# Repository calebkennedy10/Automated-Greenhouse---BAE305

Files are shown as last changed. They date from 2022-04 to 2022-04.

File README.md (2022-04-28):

# BAE305_Project_Greenhouse
## Summary
The purpose of this project is to utilize electronics and sensors to automate several greenhouse functions on a model scale as both a prototype for a full-size microcontroller-based automation system and as an educational model that can be used to demonstrate how an automated greenhouse works. Our team developed a sensor to detect light level and utilized an affordable off-the-shelf temperature and humidity sensor in order to direct automated heating, cooling, and lighting systems, as well as an automated irrigation system running on a timer. The main goals of the project were to create code that used sensor data to activate several of the systems both for demonstration purposes and actual utilizing of the greenhouse; to assemble a suitable greenhouse setup from a clear tub; and to organize the system in a way that would provide accurate data on greenhouse conditions. Each component was tested separately and as a whole, and the automated greenhouse was able to function as outlined in the project backlog.
## Design Description
### Supplies Needed
- SparkFun Electronics RedBoard DEV-13975
- Clear storage tub
- Adafruit 997 (Plastic Water Solenoid Valve - 12V -1/2" Nominal)
- ElectricSolenoidValves.com RSC-A2-12VDC (1/4" 12V DC Push Connect Plastic Solenoid Valve)
- MXC 1/4" Automatic Drip Mist Irrigation Kit (Model: GGOB)
- SparkFun Generic Servo Motors (ROB-09065)
- Bonsai wire
- Jumper wires (male-male and male-female)
- Electrical tape
- Plusivo Hook-up Wire Kit
- Photoresistor
- Ws2812 LED Matrix Panel
- DC 12V to 5V Converter
- 1/2" PVC pipe and various 1/2" fittings
- 10W 110V AC aquarium pump with 1/2" ID tubing output
- 1/2" ID tubing and barb fittings
- PVC cement and primer
- PLA filament
- 300W 12V power supply
- Solder
- Various crimp on electrical connectors (female disconnects, spade tongue, splices)
- 5 Gallon Bucket
- 2x Horizontal Float Switches
- 2x 12V PC fans
- Adafruit SHTC3 Temp and humidity sensor with wiring harness.
- 1/8W resistors (10K and 330)
- Fdit PTC Car Fan Air Heater for Small Room Space (12V 100W)
- TIP 31C Transistor 
- 12VDC, 30/40A Automotive Relay
- Bracket mount for relay
- Super glue

### 3D-Printed Components
All 3D printed componets are available via the "3D PRINTED PARTS" file in the repository.  They are available in their native SOLIDWORKS CAD formats.  Please refer to the assembly files in order to determine which parts are to be printed for each assembly and how the parts are assembled together.  3mm self tapping screws and 1/4"-20 bolts and nuts are the only pieces of hardware required to assemble each 3D printed assembly.  Parts can be printed out of several different materials and are designed to be printed on an FDM 3D printer.  Our team utilized Overture PLA Filament to print the parts; however, other common filaments types such as PETG, ABS, and ASA are acceptable if so desired.  All parts should be printed at a .2mm layer height with and infill density of 10%-15%.  It is advised to make spares of smaller parts such as the water emitters and servo attachments as these parts are easy to break during the assembly process.  Moving parts such as the vent flaps s will have to be sanded in order to allow for smooth rotation.  It is also recommended to drill out or sand holes where rotation will take place.  It is recommended to use a printer with a build plate area of at least 220mm x 220mm when printing large parts such as the vent flaps for the multivent.
### Circuit
While the circuit for this project is not overly complex, there is a lot of wiring involved.  Please refer to the schematic below when wiring up the system.  It is recommend that soldered connections with heat shrink coverings be utilized where possible in order to provide a water-tight seal around connections.  The power supply, voltage converter, microcontroller, breadboard, and relays should all be placed in a sealed container to protect them from the elements.  Our team utilized a 50W laser cutter to create a box to store all of these components.  If you have access to this type of tooling and wish to use our plans, the files for the box can be found in this repository.  Otherwise, any container or self-fabricated box will do as long as it provides adequate protection. 

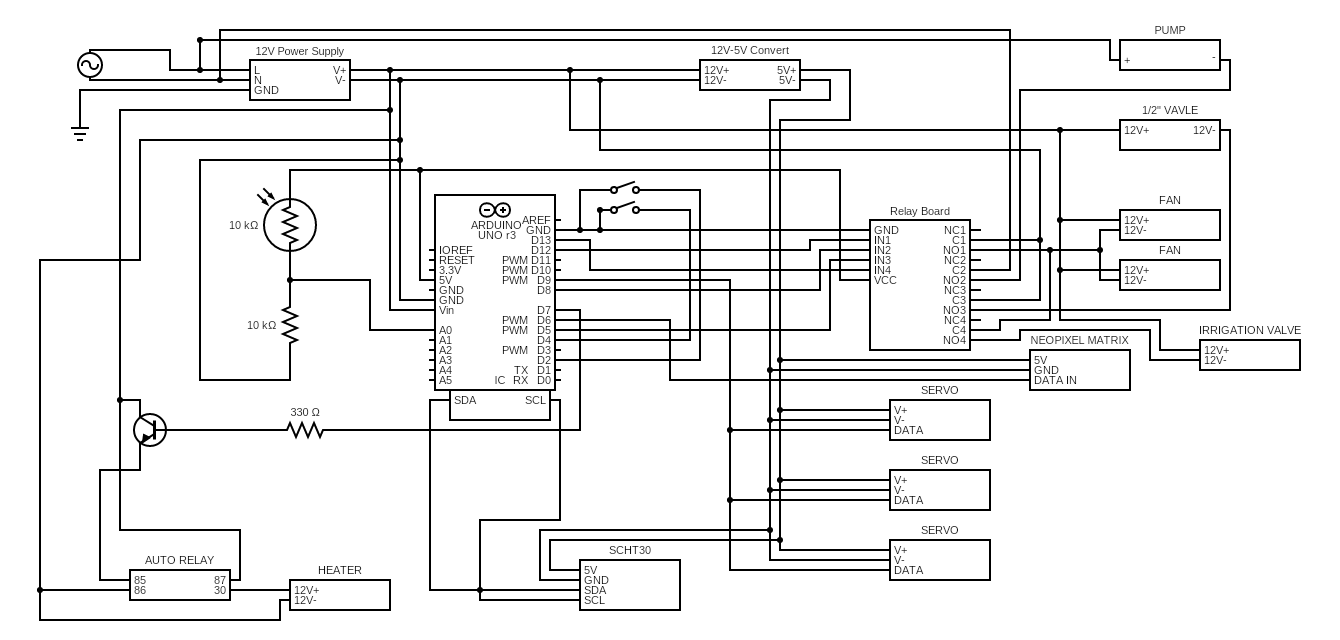
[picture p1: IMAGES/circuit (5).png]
Circuit Diagram


### Greenhouse Assembly
#### Cooling System
(The plumbing instructions for this section are intentionally a little vague.  There are multiple ways to plumb this system, and our team believes that it is best for plumbing system to be custom fabricated for each application of this design.)

Two vent fan assemblies and one evaporative cooling system assembly are required to complete the cooling system.  As mentioned previously, please refer to the SOLIDWORKS assembly files in order ot determine all 3D printed parts of the required to complete these assemblies.  The vent fan assemblies will be mounted on one end of the greenhouse while the evaporative cooling assembly will be mounted on the other side.  Assemble all sub assemblies prior to installation using 3mm screws.  Use the mounting adapters for the all of the assemblies to mark the holes that will need to be drilled in the house to mount the components.  All mounting holes will use 1/4"-20 hardware to hold components in place

Use the 5 gallon bucket to make a water sump for the evaporative cooling system.  Mount the pump at the bottom of the bucket.  Then mount a horizontal float switch 1 to 2 inches above the pump and mount another float switch approximately 6 inches below the top of the bucket.  Mount the 1/2" solenoid valve to the side of the bucket or in a pemanent location close by.  An input line that accepts a pressurized water source, such as a garden hose, will need to fabricated based on application needs.  An output line that runs from the valve to the inside of the sump will also need to be made.

For the vent fan assemblies, try to mount them as close to the center as possible to allow room for the servo mounts on the inside of the house.  One mounting adapter, the fan mount, fan, and fan retainer go on the exterior of the house while the other adapter, vent assembly, and servo mount go on the interior.  Once the proper orientation of the fan is decided on, drill a 5/16" hole in the fan mount to allow for the wires to pass through the wall of the mount.  This mounting procedure is to be utilized for both vent fan assemblies.

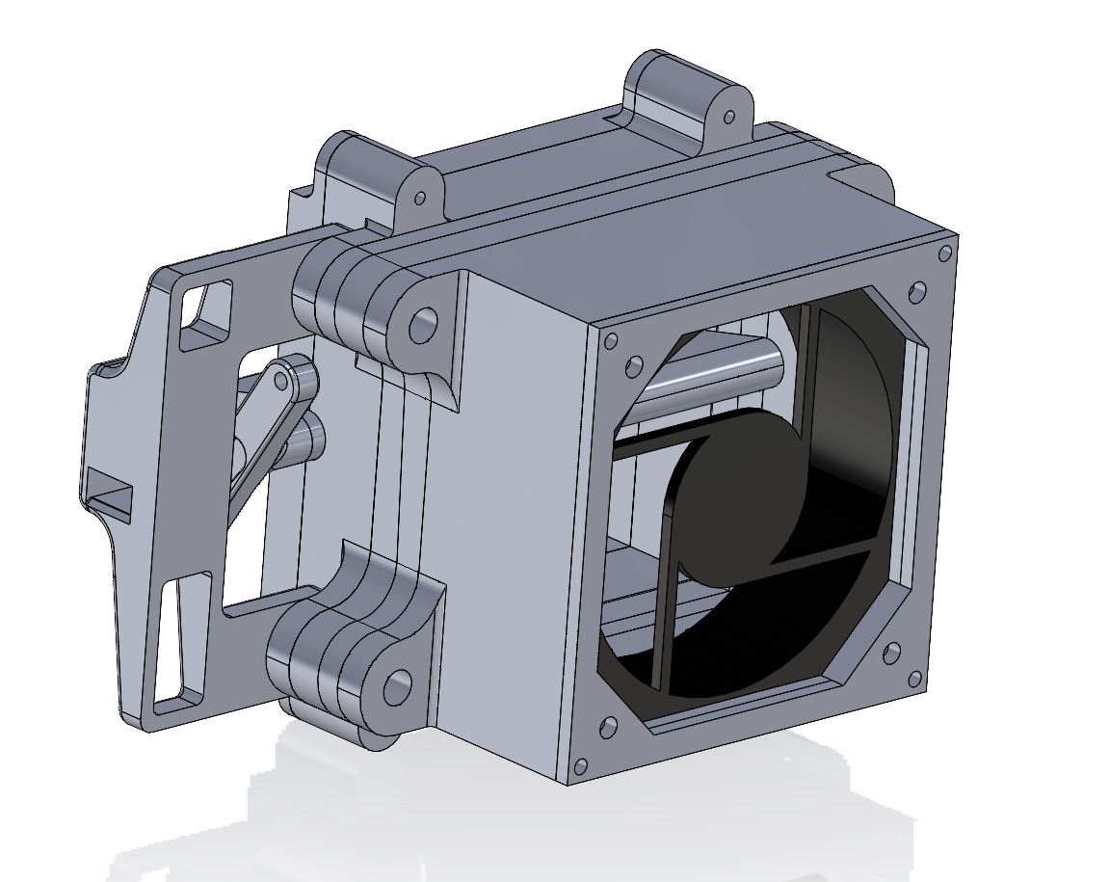
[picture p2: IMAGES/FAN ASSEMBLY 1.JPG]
Fan Assembly

(Fan Vent Assembly-Exterior View)
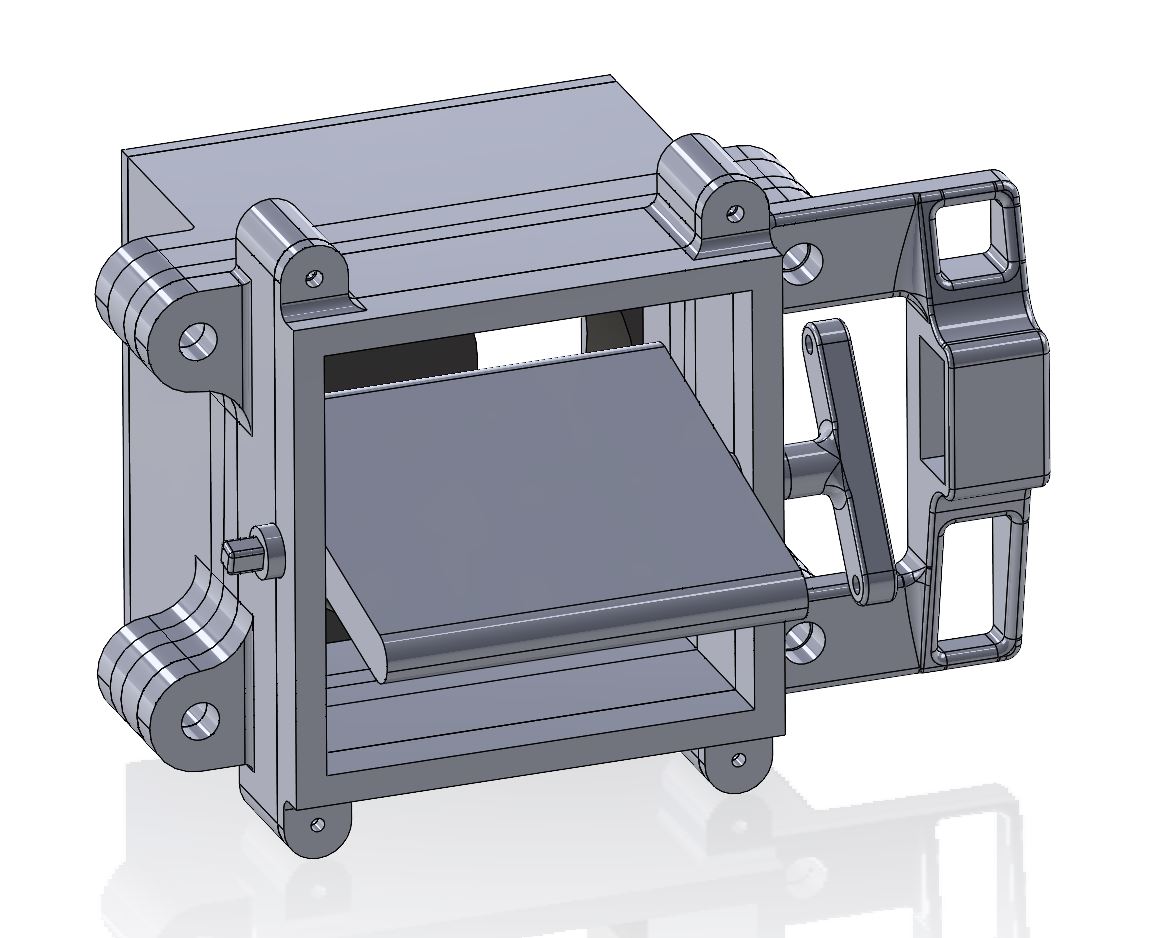
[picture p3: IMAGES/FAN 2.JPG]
Fan 2 Assembly

(Fan Vent Assembly-Interior View)

For the evaporative cooling system assembly, mount it as far to one side of the house as possible to allow for enough room for the servo mount on the inside.  The evaporative cooling wall assembly and one set of mounting adapters are mounted to the exterior of the greenhouse while the multi-vent assembly, servo mount, and last set of mounting adapters are mounted on the inside of the greenhouse.  The supply pipe for the evaporative cooling will need to fabricated using 1/2" PVC pipe, 15 Water Emitters, a PVC end cap, a slip joint-female thread pvc fitting, and male thread-1/2" barb fitting.  The 3/16 jig in the 3D printed parts folder can be used along with a cordless drill and 3/16" drill bit to drill the holes for the emitters.  The jig is used by inserting the peg into the first drilled hole and then drilling the next hole through the opening in the jig.  This process can be repeated for all 15 holes.  After drilling all of the holes, prep the pipe with primer, and insert the water emitters into the holes.  Use PVC cement on the emitter when placing them on the pipe to adhere them to the pipe and create a water tight seal.  Then slide the 3D printed pipe mounts onto both ends of the pipe.  Mount the pipe on the greenhouse and cut the ends to your desired length.  Then use the primer and cement to put on the rest of the fittings. 1/2" tubing will have to be ran from the pipe to the pump in the water sump; therefore, the last fitting on the pipe whould be a 1/2" barb fitting with a hose clamp
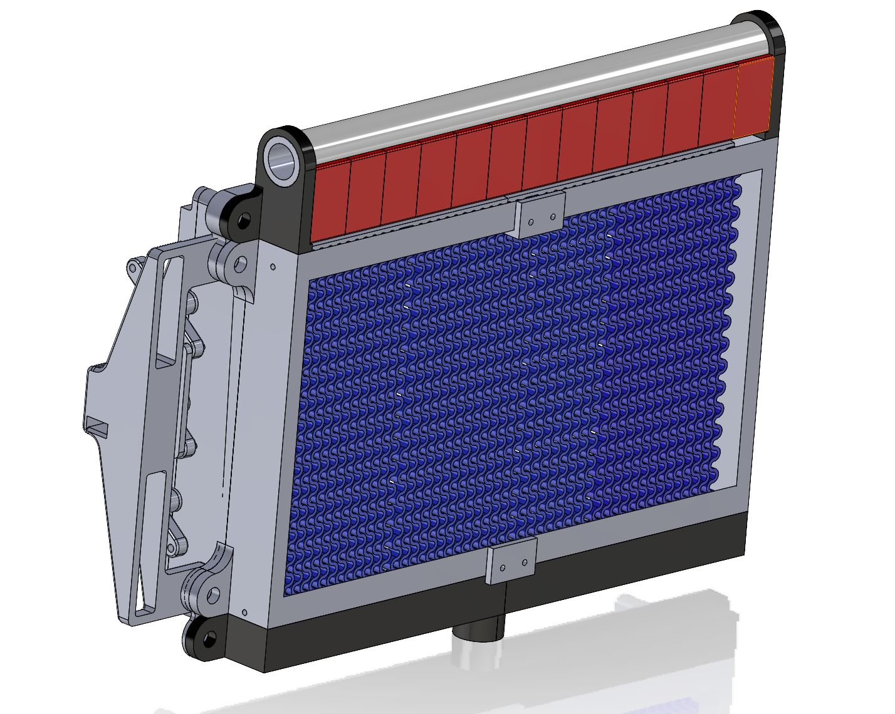
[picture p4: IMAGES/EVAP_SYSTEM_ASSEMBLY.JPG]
Evaporative Cooling Assembly

(Evaporative Cooling Assembly)

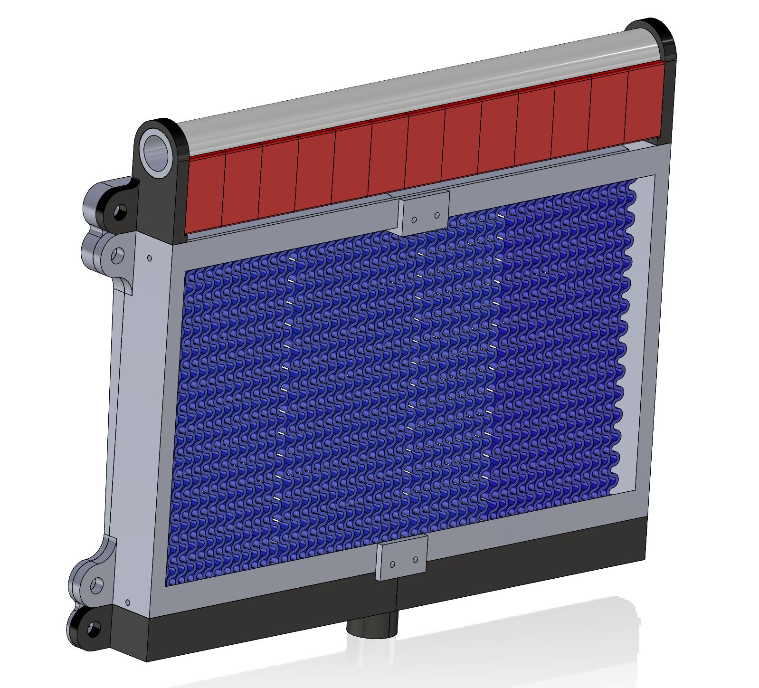
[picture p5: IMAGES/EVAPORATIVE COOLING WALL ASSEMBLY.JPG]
Evaporative Cooling Wall

(Evaporative Cooling Wall)

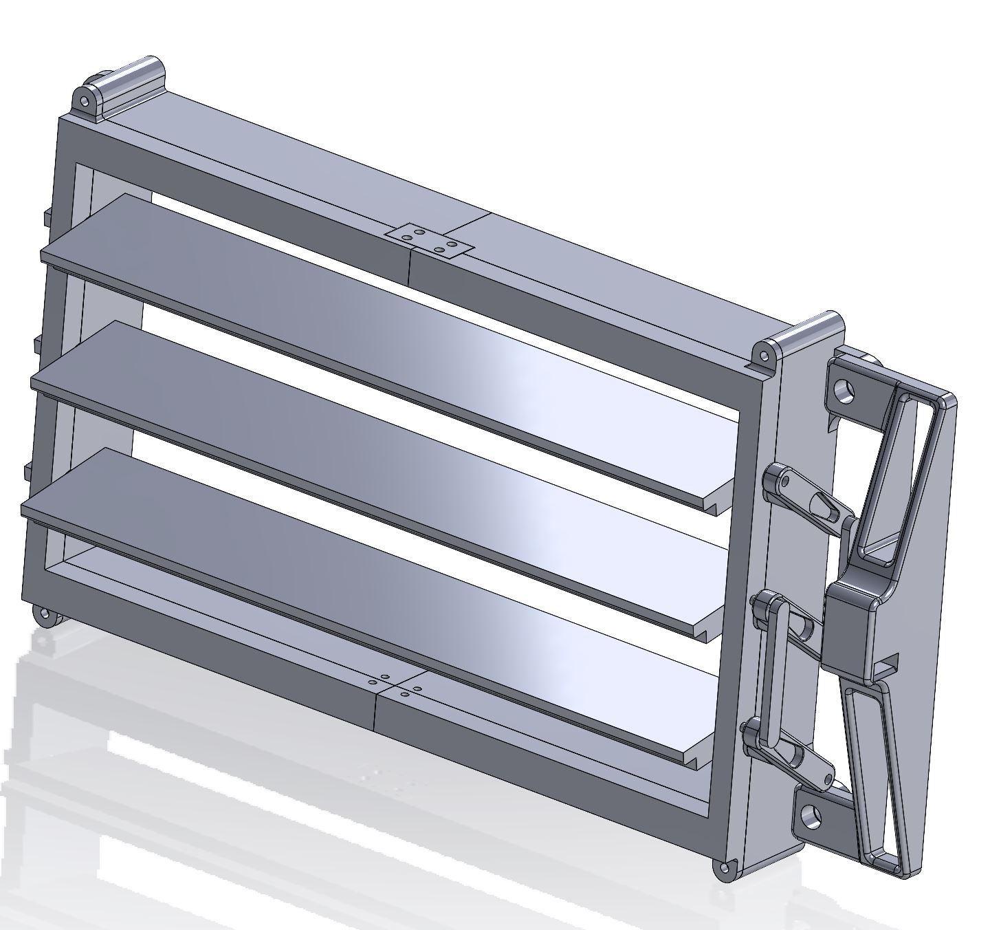
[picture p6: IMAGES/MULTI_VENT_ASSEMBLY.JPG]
Multi-Vent Assembly

(Multi-Vent Assembly)

Finally, use an Arduino to set three servo motors to 30 degrees.  Then press a servo arm into three 3D printed servo attachments.  Put the servo attachments on the ends of the vent flaps.  For the multi-vent assembly, a servo attachment will need to be added to both the lower and upper vent flap.  All three attachments will have to be connected using the vent links in the orientation shown by the picture above.  Once the links are in place, use a soldering iron to melt and expad the ends of the links to keep them from slipping out of the servo attachements.  Finally, mount all three servos using the servo mounts.
#### Heating System
The heater was purchased from amazon and consists of two parts: the electric heating element and fan. To simplify the wiring and to ensure that the fan and heating element would be on at the same time, the ground and power wires for each component were spliced together. The heater was mounted to the middle of the tub perpendicular to the cooling system using nuts and bolts, which allows for the cooling system to have ample space. Other components associated with system was a TIP 31C transistor, 1kΩ resistor, and an automotive relay (12 VDC, 40A) and are housed in the electronics housing. The automotive relay’s 85 output pin is wired to the transistor's middle pin on the breadboard and then the transistor's base pin is wired to the Arduino so that the heating system can be controlled. The system required various crimp on electrical connectors such as female disconnects, splices, and spade tongues to wire these components together. This system is wired according to the provided schematic above.
#### Lights
The parts needed for the lighting system are the Ws2812 LED matrix panel, DC 12V to 5V converter, photoresistor, wires, a resistor, 12V power supply, and Arduino. The voltage converter and Arduino are placed in the electronics housing. The LED matrix is or glued in place on the top exterior of the greenhouse. Two 1/16-inch holes are drilled into the top of the of the electronics housing. The two photoresistor wire ends are put through these two holes with the light sensing part of the photoresistor on the exterior. The other resistor is placed on the Arduino breadboard. All the components are wired according to the schematic.
#### Sensors
The sensor systems for this project is rather simple.  The first system is a voltage divider that uses a photoresistor to act as a light detection system.  The voltage divider is supplied with 5V that passes through the photoresistor then a 10k ohm resistor which is connected to ground.  A jumper wire is connected at the node between the two resistors and is connected to the A2 pin on the microcontroller.  The controller collects the data from this sensor using the analogRead command and stores it in a variable that can be compared to a constant in order to determine if the lighting system should be on or off.  The photoresistor itself should be placed in a fully exposed area in order to properly monitor the sunlight level.  For our application, we placed it on the top of our electronics box.

The second sensor is the Adafruit SHTC3.  This sensor is a compact temperature humidity sensor that utilizes a simple JST wiring harness and I2C communication protocol.  Adafruit has a library developed specifically for this sensor that allows for quick and easy data collection via the I2C ports on the SparkFun Redboard.  The data collected from the sensor is converted to an integer type variable that can be used in logic statements to determine which controlled environment systems should be turn on or off in order to maintain the optimum in door conditions for plant growth.  The sensor was mounted to the inside of the greenhouse using the 3D printed temp sensor mount, 3mm self-tapping screws, and super glue.  The sensor was screwed on to the mount.  Then the back of the mount was glued to the inside wall of the greenhouse close to the exhaust fans.

#### Irrigation
The irrigation system consists of a 1/4" 12V DC plastic solenoid valve, as well 15 feet of 1/4" diameter tubing, 18 adjustable mister nozzles, 20 flat tee fittings, and a 3/4"-1/4" faucet adapter from the MXC Automatic Drip Mist Irrigation Kit. It is split into three lines across the length of the ceiling of the greenhouse, which are attached via twelve loops of bonsai wire strung through pairs of holes drilled into the ceiling. Each line contains 6 mister nozzles, which are attached to flat tees with 1/2" lengths of tubing; tubing is also used to string the flat tees together in order to create an irrigation line. 2 other flat tees are used to connect the lines to each other and to the tubing that goes to the solenoid valve. All connection of tubing to tees should be done using a butane torch to soften the tubing for easier insertion. The solenoid valve can also be connected to the faucet adapter via a portion of tubing, and then wired to the power supply and relay using male-to-female jumper wires. The wires should be soldered to the tabs on the valve: the left wire to power and the right to the relay. The faucet adapter should be used to connect the irrigation to an outside water supply, such as a faucet or hose.

### Code

#### Demo Code

This code was designed to test and demonstrate the functioning of the different subsystems. This was done so there was not a need for a change in the environment for the sensors to pick up on to turn on the different subsystems. To do this, a serial monitor was set up. It asked for the desired temperature and humidity, and status of lights and irrigation. Based on these inputs, logic if-else statements turned on or off the different subsystems. This allowed for easy turning on or off of the different subsystems to see or show if they worked individually and all together. 

`#include <Servo.h>`

`String temperature;`

`String RH;`

`String light;`

`String irrigation;`

`int temperatureInput;`

`int RHInput;`

`int lightInput;`

`int irrigationInput;`

`int lowWaterPin = 2;`

`int highWaterPin = 4;`

`int refillValve = 5;`

`int heaterPin = 7;`

`int pumpPin = 8;`

`int fanPin = 12;`

`int irrigationPin = 13;`

`int ventOne = 9;`

`Servo servoOne;`

`#include <Adafruit_NeoPixel.h>`

`#ifdef __AVR__`

`  #include <avr/power.h>`

`#endif`

`#define LED_PIN 3`

`#define NUMPIXELS 64`

`Adafruit_NeoPixel pixels(NUMPIXELS, LED_PIN, NEO_GRB + NEO_KHZ800);`

`#define DELAYVAL 500`

`void setup() {`

`  // put your setup code here, to run once:`

`  #if defined(__AVR_ATtiny85__) && (F_CPU == 16000000)`

`  clock_prescale_set(clock_div_1);`

`  #endif`

`  pixels.begin();`

`  pinMode(lowWaterPin, INPUT_PULLUP);`

`  pinMode(highWaterPin, INPUT_PULLUP);`

`  pinMode(refillValve, OUTPUT);`

`  // pinMode(LEDPin, OUTPUT);`

`  pinMode(heaterPin, OUTPUT);`

`  pinMode(pumpPin, OUTPUT);`

`  pinMode(fanPin, OUTPUT);`

`  pinMode(irrigationPin, OUTPUT);`

`  digitalWrite(refillValve, HIGH);`

`  digitalWrite(heaterPin, LOW);`

`  digitalWrite(pumpPin, HIGH);`

`  digitalWrite(fanPin, HIGH);`

`  digitalWrite(irrigationPin, HIGH);`

`  servoOne.attach(ventOne);`

` // servoTwo.attach(ventTwo);`

` // servoThree.attach(ventThree);`

`  servoOne.write(120);`

 `// servoTwo.write(0);`

 `// servoThree.write(0);`

 ` Serial.begin(9600);`

 ` Serial.println("Enter demo parameters.");`

 ` Serial.println("Seperate parameter values with commmas. Only input integers");`

 ` Serial.println("Input order: Temperature, Relative Humidity, Light Status, Irrigation Status");`

 ` Serial.println("Appropriate input values:");`

 ` Serial.println("  Temperature: Anything in Degrees Fahrenheit");`

 ` Serial.println("  Relative Humidity: 0-100");`

 ` Serial.println("  Light Status: 1 = Turn on, 0 = Turn off");`

 ` Serial.println("  Irrigation Status: 1 = Turn on, 0 = Turn off");`

 ` Serial.println("Example Input: 80,60,1,1");`

`}`

`void loop() {`

`  // put your main code here, to run repeatedly`

`  if (Serial.available()>0) {`

`    temperature = Serial.readStringUntil(',');`

`    RH = Serial.readStringUntil(',');`

`    light = Serial.readStringUntil(',');`

`    irrigation = Serial.readStringUntil(',');`

`    temperatureInput = temperature.toInt();`

`    RHInput = RH.toInt();`

`    lightInput = light.toInt();`

`    irrigationInput = irrigation.toInt();`

`      if (lightInput == 1) {`

`        pixels.fill(pixels.Color(255, 0, 255), 0, 64);`

`        pixels.show();    `

`      }`

`      else {`

`        pixels.fill(pixels.Color(0, 0, 0), 0, 64);`

`        pixels.show();`

`      }`

`      if (irrigationInput == 1) {`

`        digitalWrite(irrigationPin, LOW);`

`      }`

`      else {`

`        digitalWrite(irrigationPin, HIGH);`

`      }`

`      if (lowWaterPin == HIGH) {`

`        digitalWrite(refillValve, LOW);`

`          while (highWaterPin==HIGH) {`

`            delay(1000);`

`          }`

`        digitalWrite(refillValve, HIGH);  `

`      }`

`      if (temperatureInput > 85) {`

`        servoOne.write(30);`

`        delay(2500);`

`        digitalWrite(fanPin, LOW);`

`        digitalWrite(pumpPin, LOW);`

`        digitalWrite(heaterPin, LOW);`

`      }`

`      else if (temperatureInput > 75 & RHInput< 50){`

`        servoOne.write(30);`

`        delay(2500);`

`        digitalWrite(fanPin, LOW);`

`        digitalWrite(pumpPin, LOW);`

`        digitalWrite(heaterPin, LOW);`

`      }`

`      else if (temperatureInput > 75) {`

`        servoOne.write(30);`

`        delay(2500);`

`        digitalWrite(fanPin, LOW);`

`        digitalWrite(heaterPin, LOW);`

`        digitalWrite(pumpPin, HIGH);`

`      }`

`      else if (temperatureInput < 55) {`

`        servoOne.write(120);`

`        delay(2500);`

`        digitalWrite(heaterPin, HIGH);`

`        digitalWrite(fanPin, HIGH);`

`        digitalWrite(pumpPin, HIGH);`

`      }`

`      else{`

`        servoOne.write(120);`

`        delay(2500);`

`        digitalWrite(fanPin, HIGH);`

`        digitalWrite(heaterPin, LOW);`

`        digitalWrite(pumpPin, HIGH);`

`      }`

`}`

`}`

#### Automation Code

This is the true automation code for the greenhouse.  This code builds off of the demo code’s logic to create an automated system by utilizing sensor readings to control subsystems rather than utilizing a manual input from the operator.  Once again, the sensors that are utilized are the Adafruit SHTC3 temperature and humidity sensor, which operates using the I2C communication protocol, and a voltage divider circuit that utilizes a photoresistor to vary the analog input read by the Arduino according to the exterior lighting conditions.  The data collected from these sensors are stored in integer variables that are applied to logic base if, else if, and else statements to determine whether the cooling, heating, and lighting systems come on.  The irrigation system was automated through the use of a simple algorithm that use the milllis() Arduino function to turn on the irrigation system for one minute every six hours.  These intervals can easily be changed by modifying a couple of variables at the start of the code.  All variables that are utilized within in this code use a naming scheme that allows the operator to easily determine the data that is stored in the variable in order to allow for quick modifications to be made to the code in order to meet the operator’s needs.

`// variable setup`

`#include <Servo.h>`

`#include "Adafruit_SHTC3.h"`

`Adafruit_SHTC3 shtc3 = Adafruit_SHTC3();`

`#include <Adafruit_NeoPixel.h>`

`#ifdef __AVR__`

  `#include <avr/power.h>`
  
`#endif`

`#define LED_PIN 3`

`#define NUMPIXELS 64`

`Adafruit_NeoPixel pixels(NUMPIXELS, LED_PIN, NEO_GRB + NEO_KHZ800);`

`#define DELAYVAL 500`

`int tempSensPin = A0;
`
`int RHSensPin = A1;`

`int lightSensPin = A2;`

`int irrigationTime = 1;`

`int irrigationInterval = 360;`

`int irrigationStatus = 0;`

`int hours = 0;`

`int minutes1 = 0;`

`int minutes2 = 0;`

`int timePast = 0;`

`int lightThreshold = 550;`

`int temperature = 70;
`
`int humidity1 = 60;`

`int lowWaterPin = 2;`

`int highWaterPin = 4;`

`int refillValve = 5;`

`int heaterPin = 7;`

`int pumpPin = 8;`

`int fanPin = 12;`

`int irrigationPin = 13;`

`int ventOne = 9;`

`Servo servoOne;`

`void setup() {`

  `// put your setup code here, to run once:`
  
  `#if defined(__AVR_ATtiny85__) && (F_CPU == 16000000)`
  
  `clock_prescale_set(clock_div_1);`
  
  `#endif`
  
  `pixels.begin();`
  
  `pinMode(lowWaterPin, INPUT_PULLUP);`
  
  `pinMode(highWaterPin, INPUT_PULLUP);`
  
  `pinMode(refillValve, OUTPUT);`
  
  `pinMode(heaterPin, OUTPUT);`
  
  `pinMode(pumpPin, OUTPUT);`
  
  `pinMode(fanPin, OUTPUT);`
  
  `pinMode(irrigationPin, OUTPUT);`

  `digitalWrite(refillValve, HIGH);
  `
  `digitalWrite(heaterPin, LOW);`
  
  `digitalWrite(pumpPin, HIGH);
  `
  `digitalWrite(fanPin, HIGH);`
  
  `digitalWrite(irrigationPin, HIGH);`
  
  `servoOne.attach(ventOne);`

  `servoOne.write(120);`

  `Serial.begin(9600);`

  `while (!Serial)`
  
  `delay(10);     // will pause Zero, Leonardo, etc until serial console opens`

  `Serial.println("SHTC3 test");`
  
  `if (! shtc3.begin()) {`
  
  `Serial.println("Couldn't find SHTC3");`
  
  `while (1) delay(1);`
  
  `}`
  
  `Serial.println("Found SHTC3 sensor");`
  
  `Serial.println(irrigationInterval);`
`
}`

`void loop() {`

`// put your main code here, to run repeatedly:`

  `sensors_event_t humidity, temp;`

`shtc3.getEvent(&humidity, &temp);// populate temp and humidity objects with fresh data`

`lightSensPin = analogRead(A2); `

`Serial.println(lightSensPin);`

  `if (lightSensPin < lightThreshold){`

`pixels.fill(pixels.Color(255, 0, 255), 0, 64);`

`pixels.show(); `

`}`

`else {`

`pixels.fill(pixels.Color(0, 0, 0), 0, 64);`

`pixels.show();`

`}`

`if (lowWaterPin == HIGH) {`

`digitalWrite(refillValve, LOW);`

`while (highWaterPin== HIGH) {`

`delay(1000);`

`}`

`digitalWrite(refillValve, HIGH);  `

`}`

`temperature = temp.temperature;`

`humidity1 = humidity.relative_humidity;`

`Serial.println(temperature);`

`Serial.println(humidity1);`
   
`if (temperature > 29) {`
   
   `servoOne.write(30);`
   
   `delay(2500);`
   
   `digitalWrite(fanPin, LOW);`
   
   `digitalWrite(pumpPin, LOW);`
   
   `digitalWrite(heaterPin, LOW);`
   
   `}`
   `else if (temperature> 24 & humidity1 < 50){`
   
   `servoOne.write(30);`
   
   `delay(2500);`
   
   `digitalWrite(fanPin, LOW);`
   
   `digitalWrite(pumpPin, LOW);`
   
   `digitalWrite(heaterPin, LOW);`
   
   `}`
   
   `else if (temperature> 24) {`
   
   `servoOne.write(30);`
   
   `delay(2500);`
   
   `digitalWrite(fanPin, LOW); `
   
   `digitalWrite(heaterPin, LOW);`
   
   `digitalWrite(pumpPin, HIGH);`

   `}`
   
   `else if (temperature < 22) {`
   
   `servoOne.write(120);`
   
   `delay(2500);`
   
   `digitalWrite(heaterPin, HIGH);`
   
   `digitalWrite(pumpPin, HIGH);`
   
   `digitalWrite(fanPin, HIGH);`
   
   `}`
   
   `else{`
   
   `servoOne.write(75);`
   
   `delay(2500);`
   
   `digitalWrite(fanPin, HIGH);`
   
   `digitalWrite(heaterPin, LOW);`
   
   `digitalWrite(pumpPin, HIGH);`
   
   `}`

  `minutes1 = millis()/60/1000-minutes2;`
`
Serial.println(minutes1);`

`if(minutes1 >= irrigationInterval & irrigationStatus == 0) {`

`minutes2 = minutes2+360;`

`irrigationStatus =1;`

`digitalWrite(irrigationPin, LOW);`

`}`

`else if(minutes1>=irrigationTime & irrigationStatus == 1) {`

`minutes2 = minutes2+1;`

`irrigationStatus=0;`

`digitalWrite(irrigationPin, HIGH);`

`}`

`}`
## Testing Description
Early testing consisted of examining every component separately in order to ensure basic functionality, such as whether valves would open,servo motors would turn, fans would blow air, and the heater would get hot when instructed to by the code. The components were then tested in combination, when they were wired up as they would be for the greenhouse. 
### Equipment
- Laptop
- USB connector (Arduino to laptop)
- Access to a faucet/water supply
- Access to electrical outlet
- Ice
- Heat gun or other mild to moderate heat source
- Flashlight
### Procedure
•	Plug power supply power cord into wall and turn on the power supply.  Using a multimeter or voltmeter, ensure that the power supply outputs 12V and voltage converter outputs 5V.

•	Connect a water supply to the irrigation system and fill the water sump.

•	Upload the demo code to the microcontroller.

•	Leave the laptop connected via the usb cable and open the serial monitor.

•	Input the following commands:

o	90,90,0,0 : evaporate cooling wall should turn on, fans should turn on, and vents should open.

o	0,0,1,0: Cooling system should turn off, fans should close, heater should turn on,

o	70,50,0,1: Heater should turn off, lights should turn off, irrigation should turn on,

o	70,50,0,0: All systems should turn off

•	Upon passing all of these tests, upload the automated code.

•	Leave computer connected via usb cable and open the serial monitor to observe sensor outputs.

•	Manually alter the environment in the following ways:

o	Cover photoresistor: lights should turn on

o	Shine a flashlight on the photoresistor: lights should turn off

o	Use a mild heat source close to temperature sensor: cooling system should turn on, vents should open

o	Apply ice to the temperature sensor: cooling system should turn off,heater should turn on,

•	If all of these tests are successful, then the system is operating properly.

## Design Decision Discussion
#### Power Supply
The first power supply we selected was 12V/120W. It was assumed that this would be sufficient to run all the components associated with this project. This changed once the heating system was finally selected and required 100W alone. Since this took up so much of the power supply’s capacity, it was realized that it may not be able to handle every component, so the power supply was upgraded to 12V/240W.
#### Heating System
The objective for the heating system was to provide heat for when the temperature system decides that the conditions inside are too cold. Originally, building a heater was considered by using a ripple heating plate as the heating element, making a housing for said element, and utilizing a computer fan. This changed when a heater that already contained these components, was assembled for virtually the same cost, and achieved the goal of the system was found.
#### Irrigation
The objective for the irrigation system was that it would be able to spray a tray of seedlings evenly. To this end, the MIXC Mist Irrigation Kit was chosen because it contained 1/4" tubing and associated misters, tees, and adapters, which would allow the irrigation setup to be small enough to place in three rows against the ceiling of the greenhouse. This would allow the irrigation system to provide even coverage of the inside of the greenhouse. The 1/4" DC push valve was chosen because it could connect directly to the tubing and also to the adapters, and because other components of the project were already using a 12V power supply and relay module which would allow for easy activation of the valve. The irrigation system functions best when the water supply is turned on slowly, and not at full strength.
#### Exterior Walls and Encasing
The exterior of the greenhouse was made using a clear plastic tub from the hardware supply store. For a more clean looking design with more precise mounting of the additional components, a clear acrylic would be a great decision to use. For the sake of the project budget, as well as simplicity, the team chose to use the clear plastic tub for this itteration of the design. This did mean that for mounting of the components such as the heating and cooling system, the team had to make cuts to remove material from the tub. A few different problems were encountered in that process. One issue was with using a regular drill, often times the material would crack of chip, creating variations and deviation from the initial design goal. Another issue was once things began being mounted on the sides, there were a few stress fractures that were made. These are likely attributed to the weight addition outside of traditional expectation for this type of tub. It was discovered that a hot blade was the best solution for removing material. If acrylic were to be used in a different iteration of this design, the material could be easily removed using a traditional laser cutting machine.
#### Circuitry and Wiring
To house the arduino and power supply, a wooden box was made. This box was placed ontop of a lattice above the water bucket, but could be easily relocated. The goal with placing it above the water supply was to have the lid encasement be one of the highest points on the design so that the photoresistor could be placed in the lid and get a more accurate reading to know when to turn on the lighting. Additionally, this meant the photoresistor did not have to be wired far away, and prevented the need for a PCB circuit. For this first iteration of design, the team did not elect to make an additional wire encasement for the wires that had to leave the circuit box and run to the greenhouse itself. While discussions were had about each of these design components, the decision was made to leave these add-on options for future models. 

### Design/System Limitations
There are a few limitations to this design that would need to be addressed in order implement it on a larger scale application.
1. The power supply is a 12V 300W power supply.  While this works for small scale applications, larger applications with more powerful hvac systems and lighting systems would require this component to be upgraded.
2. The SHTC3 only has one I2C address associated with it. Therefore, in order to utilize more than one of these sensors, a module such as an I2C multiplexer would need ot be utilized.
3. The size of this greenhouse only supports starting seedlings or growing smaller herbs.  The overall scale of the system would have to be increased if completing an entire plant lifecycle was desired.
4. The temperature output does not modulate so in order for precise temperature control on a larger scale, more complex modifications would have to be implemented like VFD incorporation. Also due to the lack of modulation, the equipment will cycle more so the equipment will not last as long. When dealing with larger, more expensive equipment, this would be an issue.
5. A different exterior wall and encasement would be a neccessary upgrand when scaling this product. The tub exterior works, but it is also not the most visually appealing exterior and for long term continued use, the acrylic or alternative material exterior would be ideal. Another option would be a wooden frame, with each piece attached via the frame, and then encasing everything in a clear plastic tarp like material and tacking it down on the sides, making cut outs where needed for the subsystem. This would be a more budget friendly option, and would be easily replaceable if damage were to occur to the wall encasing, but would lose a lot of the stability factors that the solid plastic offers.
6. Circuitry and wiring could easily be adjusted for larger scale applications. A circuits box on one end of the green house would allow for housing of the various components (also note limitation #1 and #4), as well as a more intentional routing of the wiring, would be neccessary. If the exterior is changed in a manner similar to something suggested in limitation #5, it would be relatively simple to add wire housing along the base of the exterior. 

## Testing Results
The testing procedure described above was utilized to test our system after assembly was complete.  When issues arose, the problems were troubleshot and corrected.  The testing procedure was then restarted at the beginning.  After all of the expected outputs were observed from the different subsystems in succession without electrical or mechanical failures.  Therefore, the project was considered to be fully operational and for all functional purposes considered to complete.

## Test Results Discussion
Since the testing of each sub section showed to be fully operational, the team had minimal trouble shooting to do. One thing that was noticed is that the tightness of the nuts and bolts on the fan attachments did appear to interfere slightly with the servo’s full range of motion in opening and closing each of the fans. This was an easy thing to adjust and optimize for servo motion and then to time the servos correctly with each other since all three motors need to open and close at the same time. Another thing that was noted during the testing was that the individual systems would briefly all turn on anytime power was cycled. This was first noted when the irrigation system would spray some water without being programmed to do so when we first turned on the power source. This was determined to be caused by the fact that the systems are relay activated and the relays are individually ground actuated. No damage or adverse results are caused by this, as it is a very minimal amount of each subsystems role, so there is no concern for this causing significant changes in temperature, humidity, nor the risk of overwatering the seedlings. 

The greenhouse is best suited for trays of small plants or seedlings. This is beneficial also for starting your plants earlier in the season before weather is fully conducive for growth, allowing them to mature fully at the desired time independent of mother nature's cooperation.

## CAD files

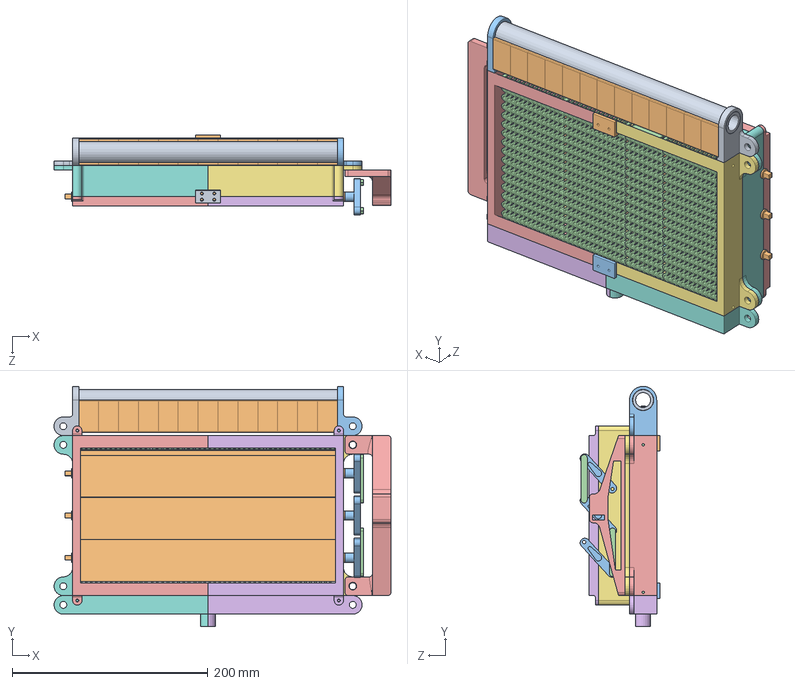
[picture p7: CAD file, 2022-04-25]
3D PRINTED PARTS/Evaporative Cooling System.SLDASM
344.5 x 245.5 x 81.5 mm
PVC Pipe
Water Emitter x 13
Pipe mount
wall insert x 3
Insert Rail Whole
Water Trench
Wall Insert Rack Mirrored
Water Trench Mirrored
Pipe Mount Mirrored
Rail Connector
Rail Connector 2
wall insert small
Multi-Vent1(Left)
Multi-Vent1(Right)
Multi-Vent2(Right)
Multi-Vent2(Whole)
Scab Plate x 2
Vent Flap 3 x 3
Servo Attachment x 3
Vent Link x 2
Servo Mount 2

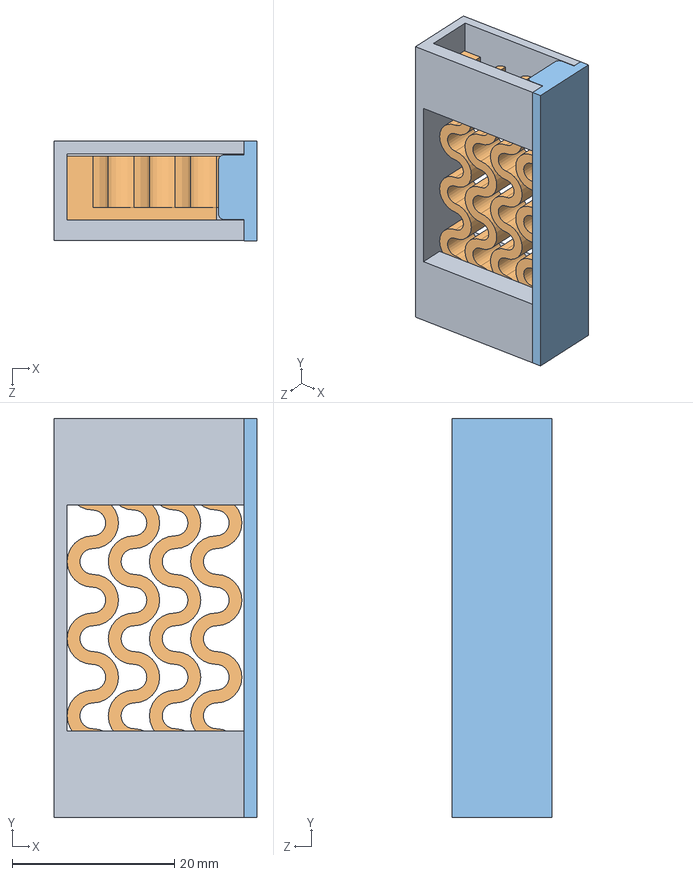
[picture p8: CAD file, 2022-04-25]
3D PRINTED PARTS/Wall Test Assembly.SLDASM
25.0 x 49.3 x 12.3 mm
Wall insert test jig
wall insert
Test Jig Cap

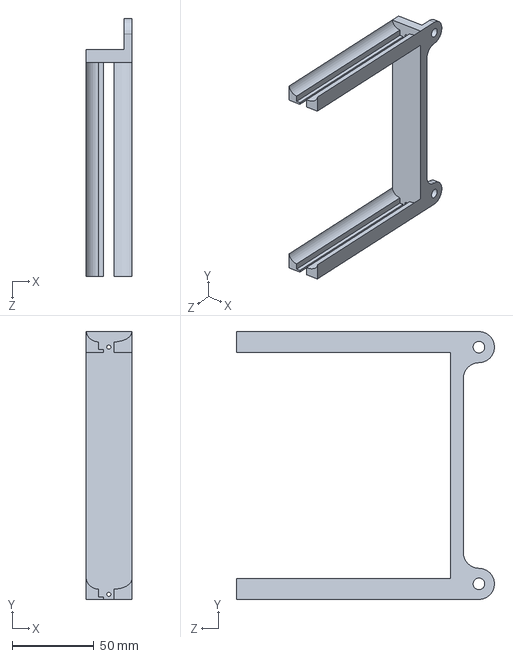
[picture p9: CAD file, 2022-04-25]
3D PRINTED PARTS/Insert Rail Whole.SLDPRT
27.9 x 163.5 x 157.5 mm

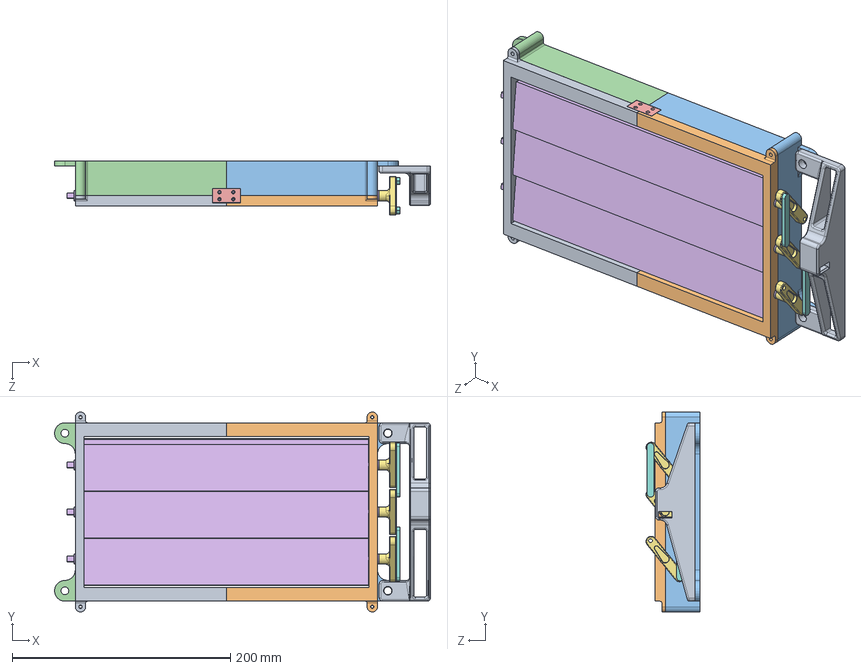
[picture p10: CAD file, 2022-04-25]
3D PRINTED PARTS/Multi-Vent Assembly.SLDASM
344.5 x 183.2 x 49.5 mm
Multi-Vent1(Left)
Multi-Vent1(Right)
Multi-Vent2(Right)
Multi-Vent2(Whole)
Scab Plate x 2
Vent Flap 3 x 3
Servo Attachment x 3
Vent Link x 2
Servo Mount 2

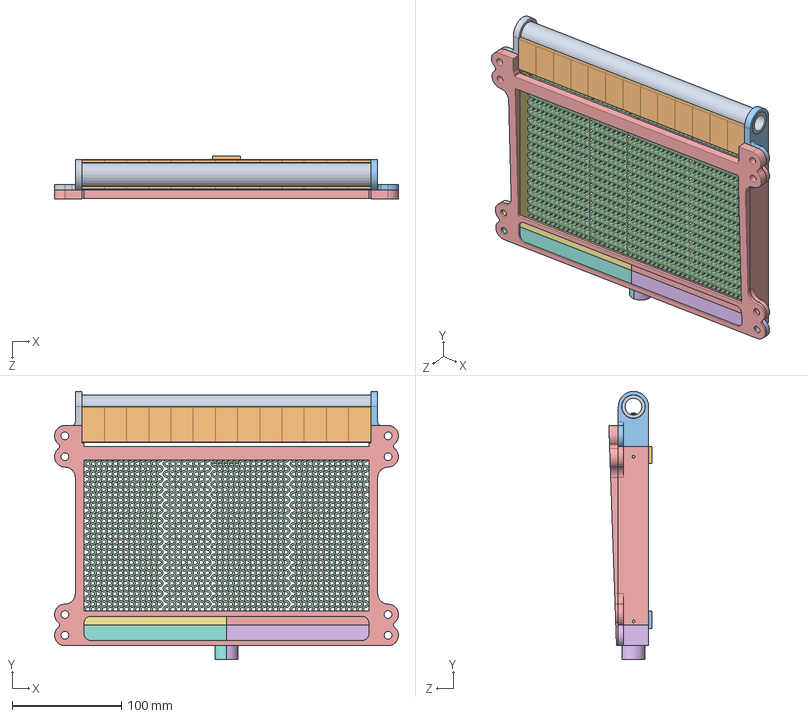
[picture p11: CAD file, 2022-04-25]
3D PRINTED PARTS/Evaporative Cooling Wall Assembly.SLDASM
315.0 x 245.5 x 39.8 mm
PVC Pipe
Water Emitter x 13
Pipe mount
wall insert x 3
Insert Rail Whole
Water Trench
Wall Insert Rack Mirrored
Water Trench Mirrored
Pipe Mount Mirrored
Rail Connector
Rail Connector 2
wall insert small

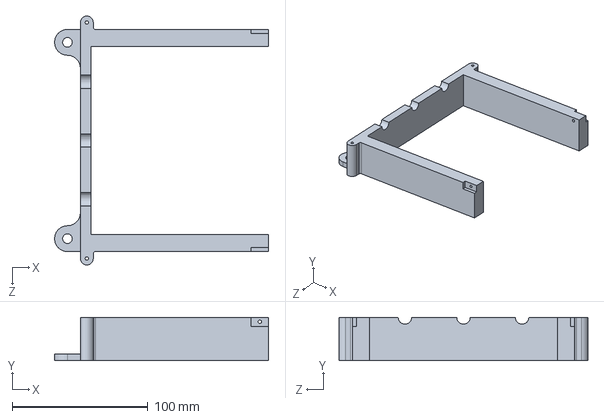
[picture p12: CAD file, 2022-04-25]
3D PRINTED PARTS/Multi-Vent2(Whole).SLDPRT
157.5 x 31.8 x 183.2 mm

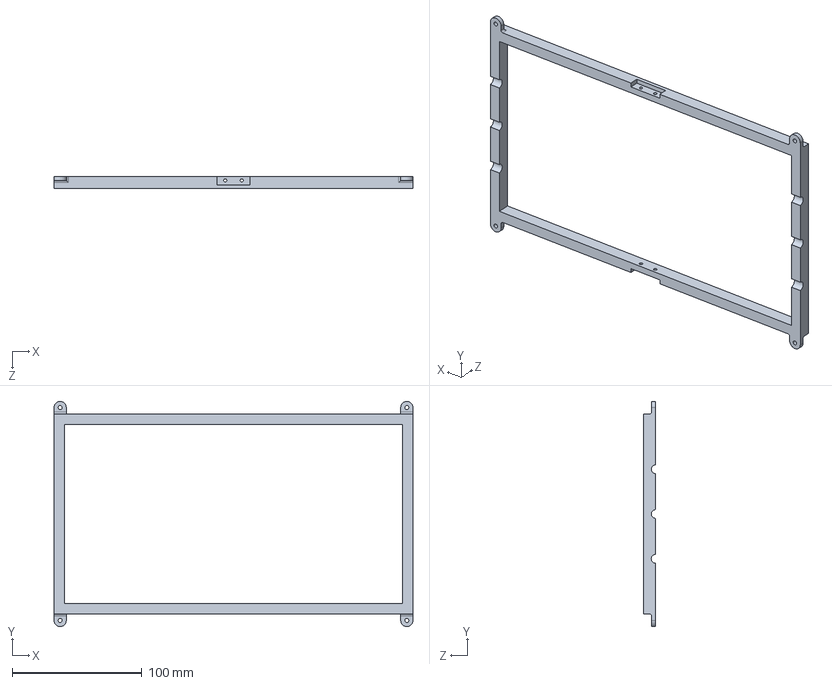
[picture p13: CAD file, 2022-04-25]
3D PRINTED PARTS/Multi-Vent1(Whole).SLDPRT
276.9 x 173.7 x 9.53 mm

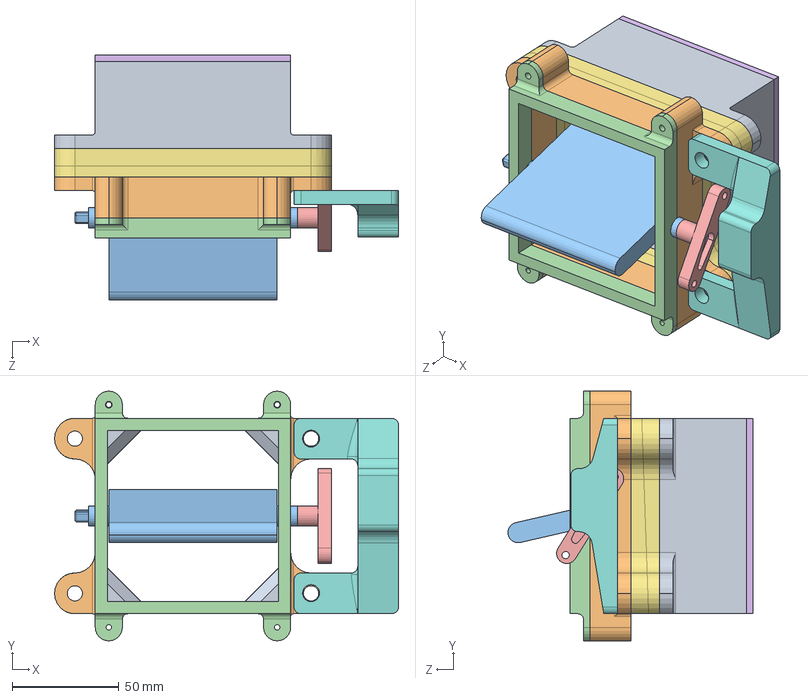
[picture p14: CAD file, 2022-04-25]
3D PRINTED PARTS/Fan Vent Assembly.SLDASM
160.9 x 116.8 x 114.7 mm
Fan Mount
Vent Mount 3
Vent Flap 2
Vent Mount 4
Servo Attachment
Fan Retainer
Mount Adapter
Servo Mount

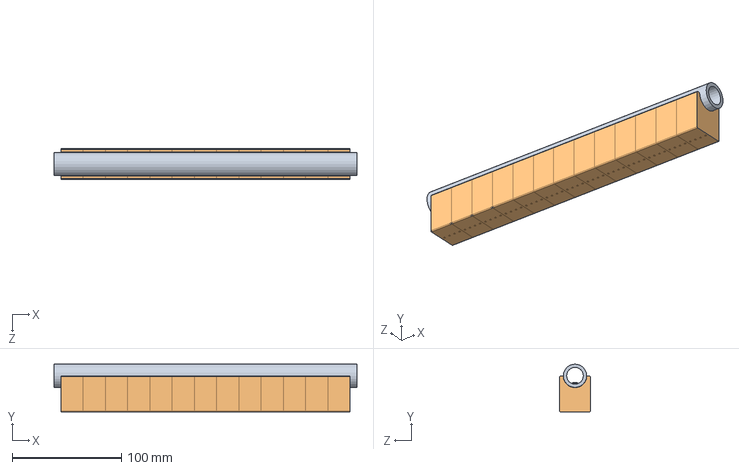
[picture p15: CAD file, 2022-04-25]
3D PRINTED PARTS/Pipe Assembly.SLDASM
276.9 x 43.7 x 27.9 mm
PVC Pipe
Water Emitter x 13

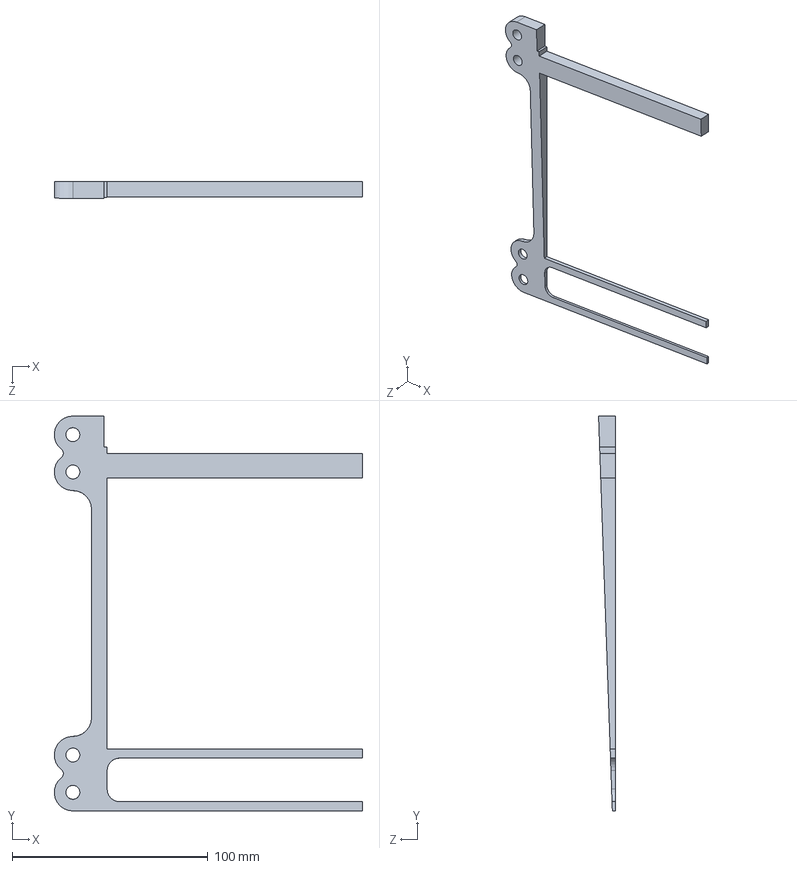
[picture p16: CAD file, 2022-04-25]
3D PRINTED PARTS/Adapter 5.SLDPRT
157.5 x 201.6 x 8.64 mm

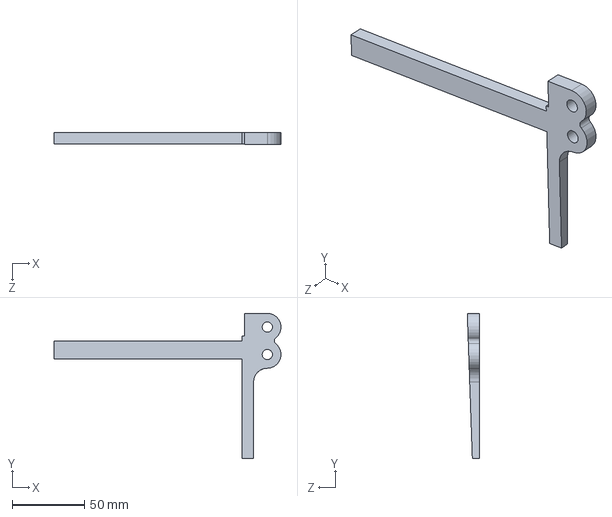
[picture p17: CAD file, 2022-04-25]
3D PRINTED PARTS/Adapter 1.SLDPRT
157.4 x 100.8 x 8.64 mm

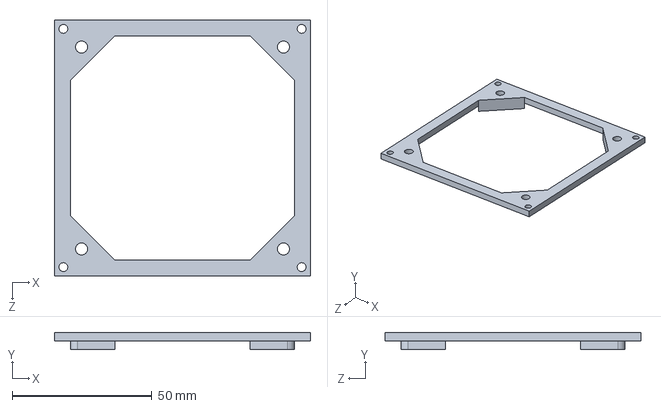
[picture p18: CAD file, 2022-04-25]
3D PRINTED PARTS/Fan Retainer.SLDPRT
91.4 x 6.22 x 91.4 mm

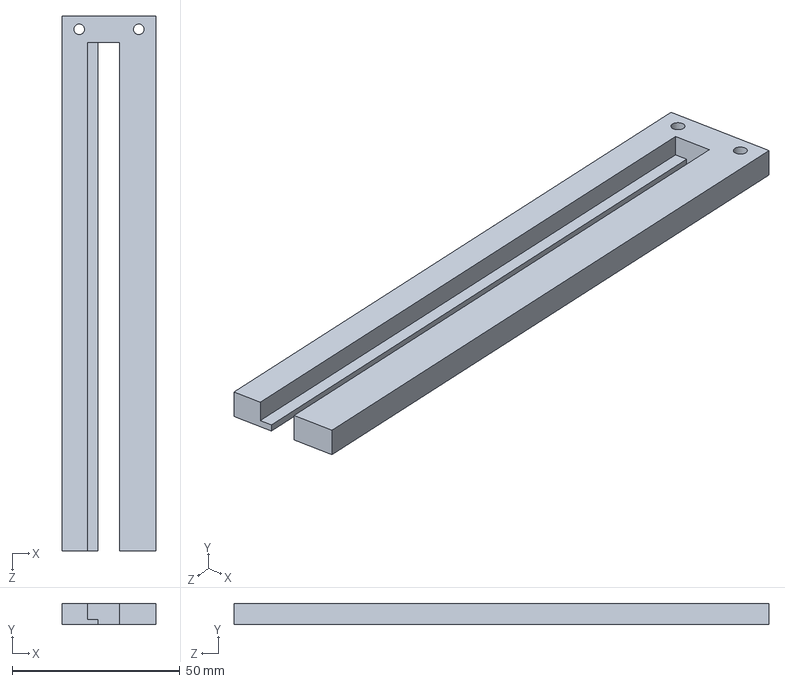
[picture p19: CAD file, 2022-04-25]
3D PRINTED PARTS/Insert Rail.SLDPRT
27.9 x 6.35 x 159.6 mm

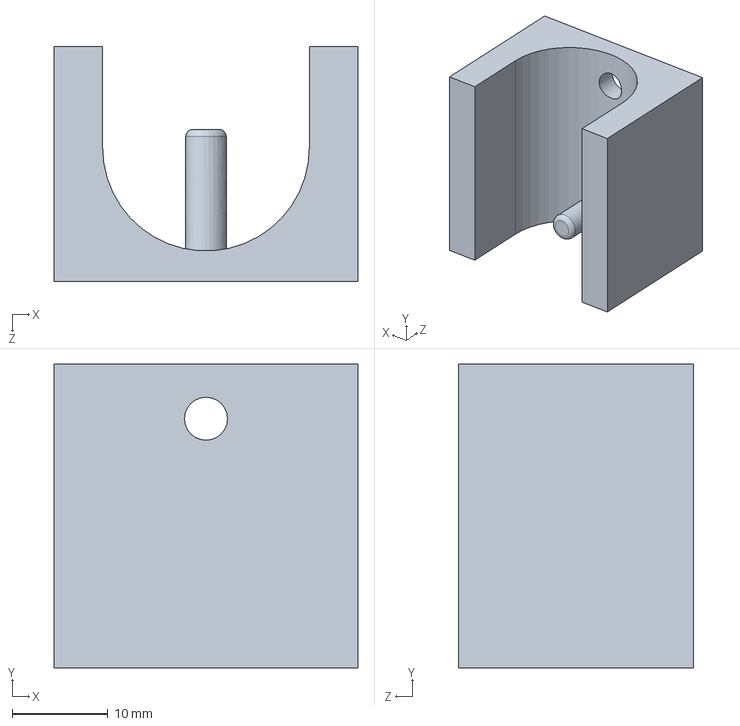
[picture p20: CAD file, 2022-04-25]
3D PRINTED PARTS/11_6_ jig.SLDPRT
31.8 x 31.8 x 24.5 mm

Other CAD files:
3D PRINTED PARTS/Water Emitter.SLDPRT
3D PRINTED PARTS/Vent Link.SLDPRT
3D PRINTED PARTS/Scab Plate.SLDPRT
3D PRINTED PARTS/Multi-Vent2(Right).SLDPRT
3D PRINTED PARTS/3_16_ jig.SLDPRT
3D PRINTED PARTS/Adapter 2.SLDPRT
3D PRINTED PARTS/Adapter 3.SLDPRT
3D PRINTED PARTS/Adapter 4.SLDPRT
3D PRINTED PARTS/Adapter 6.SLDPRT
3D PRINTED PARTS/End Cap.SLDPRT
3D PRINTED PARTS/Fan Mount.SLDPRT
3D PRINTED PARTS/Fan.SLDPRT
3D PRINTED PARTS/Insert Rail Bottom.SLDPRT
3D PRINTED PARTS/Mount Adapter.SLDPRT
3D PRINTED PARTS/Multi-Vent1(Left).SLDPRT
3D PRINTED PARTS/Multi-Vent1(Right).SLDPRT
3D PRINTED PARTS/PVC Pipe.SLDPRT
3D PRINTED PARTS/Pipe Mount Mirrored.SLDPRT
3D PRINTED PARTS/Pipe mount.SLDPRT
3D PRINTED PARTS/Rail Connector 2.SLDPRT
3D PRINTED PARTS/Rail Connector.SLDPRT
3D PRINTED PARTS/Servo Attachment.SLDPRT
3D PRINTED PARTS/Servo Mount 2.SLDPRT
3D PRINTED PARTS/Servo Mount.SLDPRT
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

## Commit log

2022-04-25 3D Printed Parts and Tools
    [11_6_ jig.SLDPRT, 3_16_ jig.SLDPRT, Adapter 1.SLDPRT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]
2022-04-27 Create Laser Cut Components
    These files were optimized for 1/4" birch wood on a 12x24" laser bed
